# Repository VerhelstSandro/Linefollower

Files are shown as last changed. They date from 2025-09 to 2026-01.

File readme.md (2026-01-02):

# LineFollower

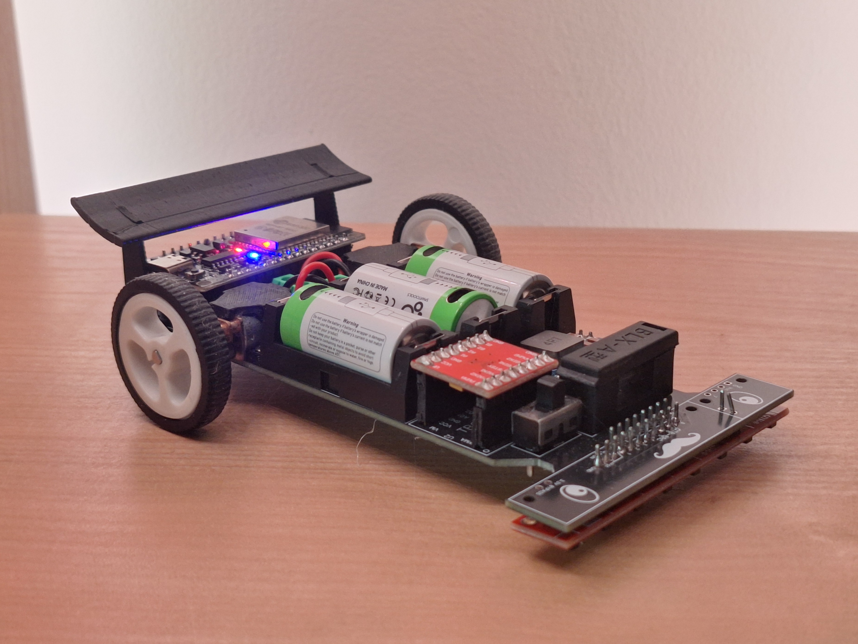
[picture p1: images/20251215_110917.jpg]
A description of my image


## specifications

microcontroller: ESP32 Wroom-32 devkit v1

motors: 12v n20 1000rpm

h-bridge: TB6612FNG

sensors: QTR-8A

batteries: RCR123A

wireless communication: ESP32

distance sensor - motors:

weight:

speed: 0.67 m/s

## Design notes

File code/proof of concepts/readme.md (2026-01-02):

# Proof of Concepts

De proof of concepts ben ik vergeten tonen in de fysieke lessen.

Bij de POC van de h brug is het enige wat niet werkt dat de linker motor niet achteruit kan draaien.
Dit komt omdat voor die motor achteruit te laten draaien er op de h brug bij Ain2 een hoog signaal moet zijn.
Deze is aangesloten op digitale pin18 van de esp en deze werkt jammer genoeg niet wanneer de SPI in gebruik is.
De SPI is in gebruik omdat ik met bluetooth werk. Ook als ik deze verwijder werkt het niet omdat de SPI automatisch opgestart wordt.

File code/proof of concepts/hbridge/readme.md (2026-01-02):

# H-Bridge proof of concept

## Werking van het programma:

1 - De linker motor gelijdelijk van stilstand tot de voorwaartse maximumsnelheid en blijft op deze snelheid draaien.

2 - De rechter motor gelijdelijk van stilstand tot de voorwaartse maximumsnelheid en blijft op deze snelheid draaien.

3 - Bijde Motoren gaan gelijdelijk stoppen.

4 - De linker motor gelijdelijk van stilstand tot de achterwaartse maximumsnelheid en blijft op deze snelheid draaien.

5 - De rechter motor gelijdelijk van stilstand tot de achterwaartse maximumsnelheid en blijft op deze snelheid draaien.

6 - Bijde Motoren gaan gelijdelijk stoppen.

en repeat

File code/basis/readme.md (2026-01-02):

## basis programma

Er is geen vershil tussen het basis programma en het finaal programma.

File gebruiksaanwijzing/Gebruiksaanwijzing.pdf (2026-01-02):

# Gebruiksaanwijzing

# Linefollower Sandro Verhelst

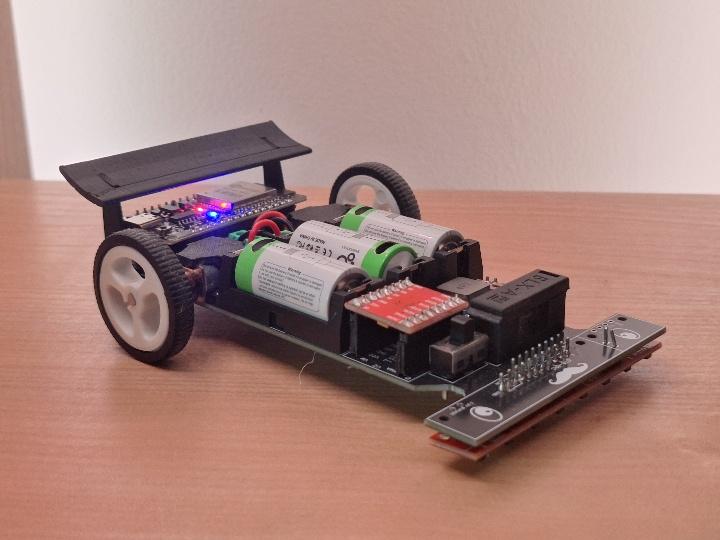
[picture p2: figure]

# Opladen / vervangen batterijen

De RCR123A batterijen die gebruikt zijn kunnen opgeladen worden via de usb-c poorten die op de batterijen aanwezig zijn met gelijk welke standaard usb-c lader.

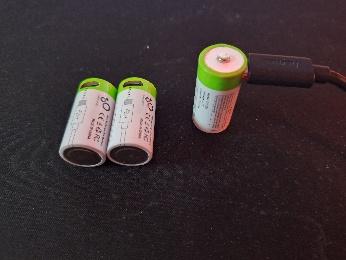
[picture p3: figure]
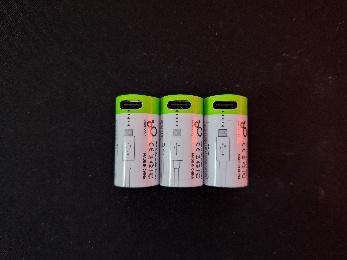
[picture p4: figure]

De batterijen zijn opgeladen zodra het rode lampje aan de plus pool groen is.

# draadloze communicatie

## verbinding maken

Voor het besturen en verbinding te maken met de linefollower is er een specifieke app gemaakt via androidstudio. De vereisten voor de app zijn simpel, een gsm met minimaal android 14.

Het APK-bestand is beschikbaar in de GitHub-repository onder de map “finaal”.
Download dit bestand naar je smartphone.

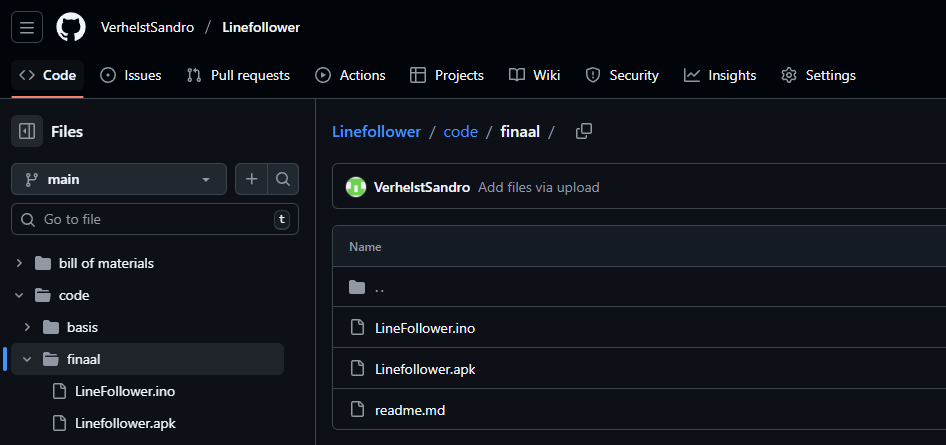
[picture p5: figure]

Open het gedownloade APK-bestand om de installatie te starten.

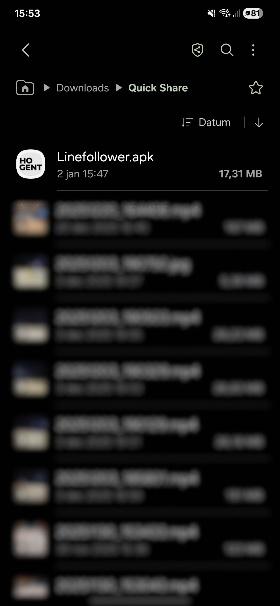
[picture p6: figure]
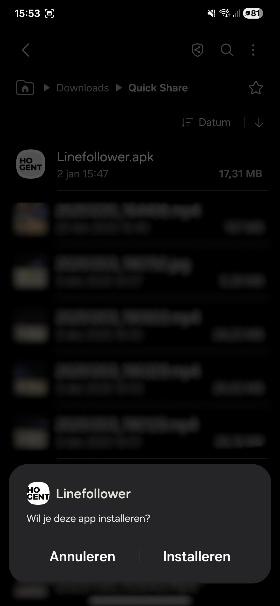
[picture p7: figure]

Bij de eerste installatie van een APK-bestand kan Android vragen om toestemming te geven aan de bestandsverkenner om applicaties van onbekende bronnen te installeren. Sta deze toestemming toe om verder te gaan.

Tijdens het installatieproces kan de antivirussoftware van de smartphone een waarschuwing weergeven. Voer in dat geval de controle uit en bevestig dat het bestand veilig is.

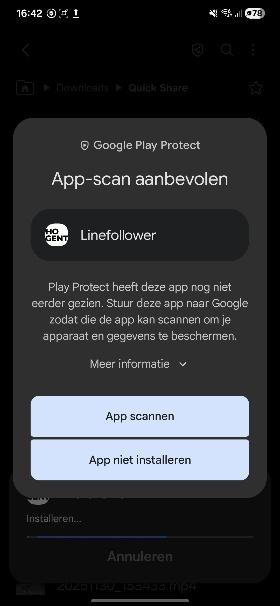
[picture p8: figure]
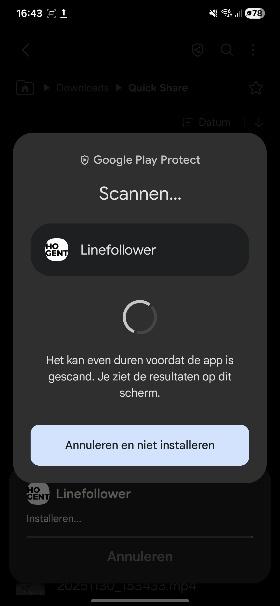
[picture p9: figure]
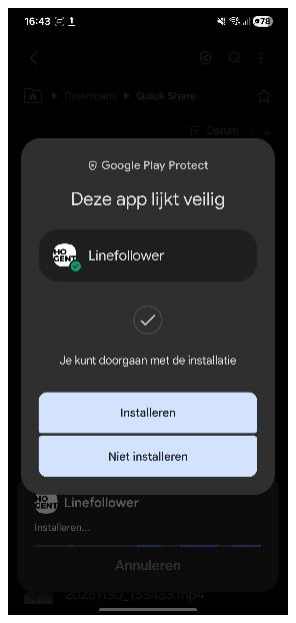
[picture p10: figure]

Na succesvolle installatie verschijnt de app in het overzicht van geïnstalleerde toepassingen.

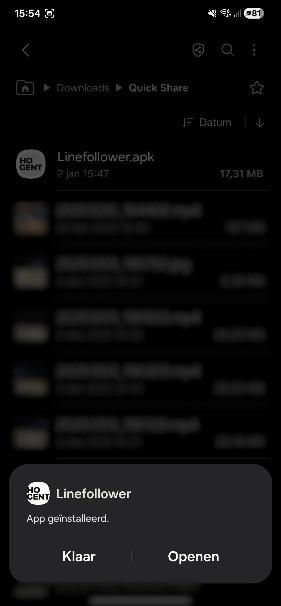
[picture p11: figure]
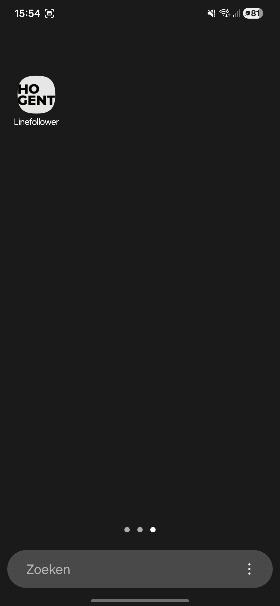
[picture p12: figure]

Zet de linefollower aan.

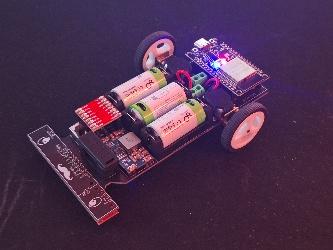
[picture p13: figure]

Activeer Bluetooth op de smartphone. Ga naar de Bluetooth-instellingen en zoek naar beschikbare apparaten. Selecteer de linefollower uit de lijst om verbinding te maken. Wanneer de verbinding tot stand is gebracht, verschijnt de linefollower als gekoppeld apparaat zonder dat die verbonden is.

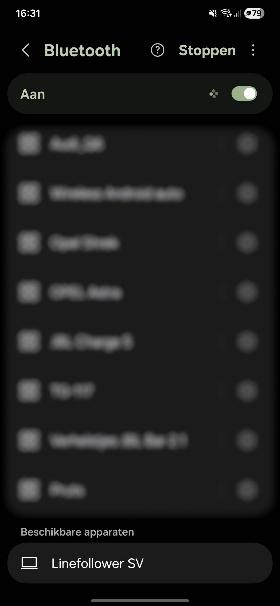
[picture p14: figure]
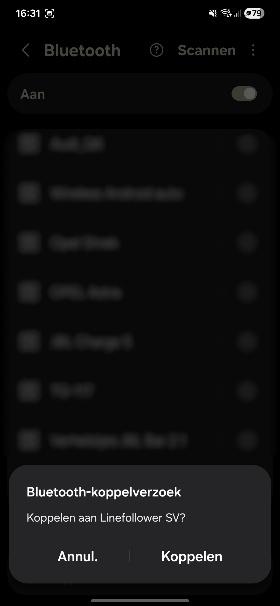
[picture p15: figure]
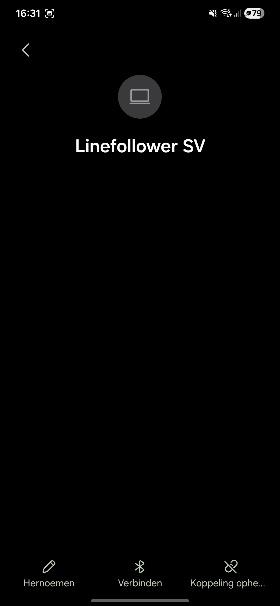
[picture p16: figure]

Open de geïnstalleerde app. Je komt terecht op het startscherm met de knop “Verbinden”. Druk op deze knop om verbinding te maken met de linefollower.

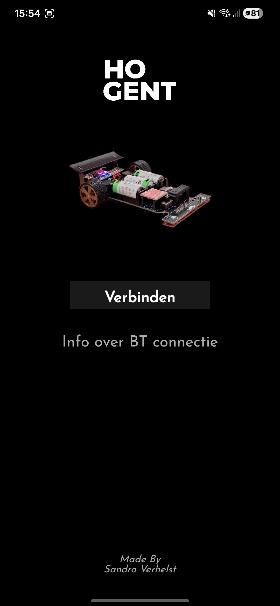
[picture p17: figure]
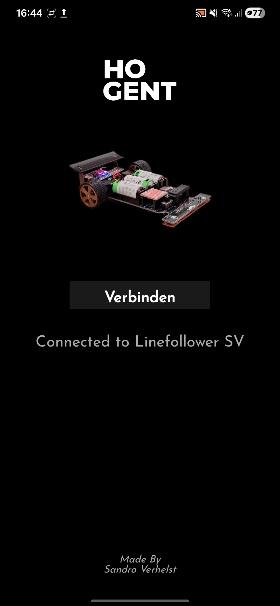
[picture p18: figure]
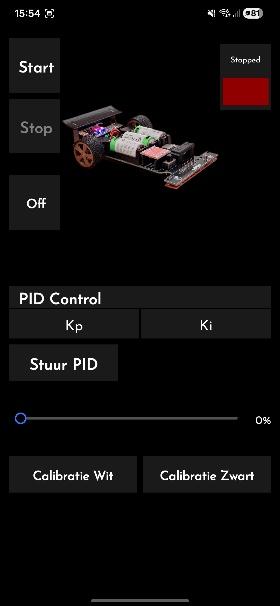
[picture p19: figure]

Na een succesvolle verbinding wordt automatisch het bedieningsscherm geopend. Vanuit dit scherm kan de linefollower volledig worden aangestuurd.

## commando's

aangezien ik met een custom app werk in plaats van commando’s ga ik gewoon uitleggen onder de commando’s hoe je dit doet in de app. Volgende foto voor referentie.

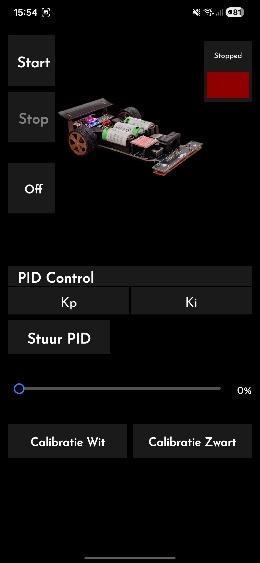
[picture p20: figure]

debug [on/off]

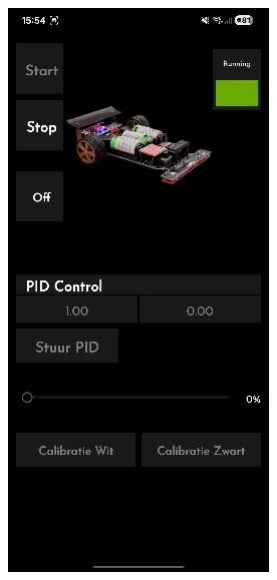
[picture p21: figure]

om te debuggen en waardes te zien moet je de via kabel de seriele poort gaan uitlezen dit kan niet via de app.

Start
Je hebt 2 mogelijkheden om start te bedienen. Start als “toggle button“ druk op start om te starten (dan kan je deze ook niet meer bedienen) en stop om te stoppen en de start knop als “dead man switch”. Door op de knop “off” te drukken toggle je tussen “off” (dead man switch off) en “hold” (hold to start). Als je nu wil starten moet je de knop blijven ingedrukt houden om de linefollower te doen rijden. Wanneer je loslaat stopt de linefollower direct.

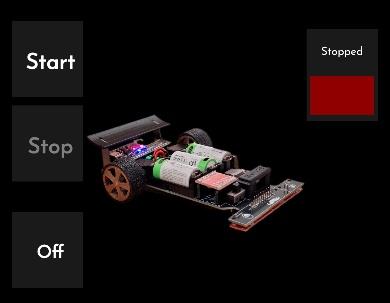
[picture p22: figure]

Stop
Je kan enkel de stop knop bedienen als de linefollower running is.

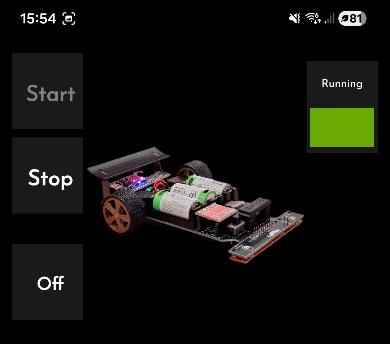
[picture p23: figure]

set cycle [µs]

Geen knop gemaakt wegens niet nodig.

set power [0..255]

Dit is in de app een slider onder stuur PID. De waarde van de snelheid is uitgedrukt in procent. Deze slider kan je niet bedienen als de Linefollower running is.

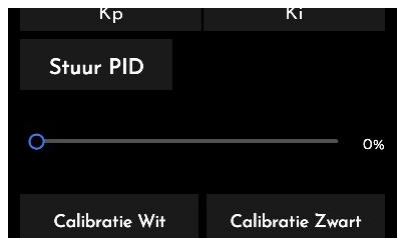
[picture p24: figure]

set kp [0..] en set ki [0..]

Deze waarden zet je door een waarde in te vullen in de vakken Kp en Ki. Door te drukken op Stuur PID worden de waarden aan de Linefollower gegeven. Deze knoppen kan je niet bedienen als de Linefollower running is.

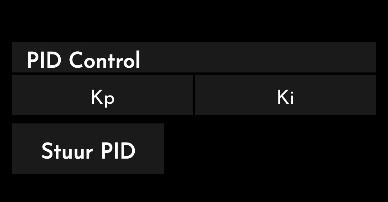
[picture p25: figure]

set kd [0..]

Geen knop gemaakt wegens niet nodig.

calibrate black en calibrate white

De twee knoppen onderaan. Door op deze knoppen te drukken kalibreer je de linefollower. De knoppen worden grijs als deze als het kleur dat de knop kalibreert al gekalibreerd is. Zo weet je dat je al gekalibreerd hebt, maar je kan de knoppen nog steeds bedienen als de linefollower niet running is.

# kalibratie

Je legt de linefollower aan en maakt verbinding via de app. Nu plaats je de robot op wit of zwart en druk je in de app op calibrate wit of calibrate zwart. Dit doe je voor bijde kleuren. Nu kan je rijden.

Indien de kalibratie die je gedaan hebt niet correct is gebeurd en je problemen ondervindt kan je steeds opnieuw op de knoppen drukken zelfs al zijn ze grijs.

De waarden worden niet opgeslaan in het eeprom geheugen omdat de app zodanig simpel is om te bedienen.

# settings

De robot rijdt stabiel met volgende parameters:

Kp = 0.9 en Ki = 0.05 bij goed opgeladen batterijen.

De robot is onder een groot bereik aan PI waardes zeer stabiel zelfs bij uitsluitend Ki (Kp = 0) met deze waarden mild beter dan de rest. Dit door een foutje in de code, het buitenste wiel gaat in een bocht sneller draaien dan de ingestelde snelheid. Dit wil zeggen dat als de snelheid over 50% gaat het buitenste wiel sneller dan 255 zou moeten draaien. Hierdoor wordt de auto boven 50% snelheid erg onstabiel. Door het grotere “potentieel” van de auto krijg je een groot bereik van PI waardes waar de auto onder 50% snelheid stabiel is.

# start/stop button

Er is geen fysieke start/stop button op de robot aanwezig.

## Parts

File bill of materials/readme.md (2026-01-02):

## bill of materials

Om de links te kunnen gebruiken moet je het bestand downloaden

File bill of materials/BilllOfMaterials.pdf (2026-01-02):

Onderdeel | Kwantiteit Prijs (€) | Link
1 | PCB Zelf Ontworpen | 1 | 1,40 | link (https://jlcpcb.com/)
2 | 12V N20 brushed DC motor 1000rpm | 2 | 4,54 | link (https://nl.aliexpress.com/item/1005005699205905.html?curPageLogUid=DE74yhz1LPuD)
3 | Esp32 WROOM-32 CH340C Type-C | 1 | 2,78 | link (https://nl.aliexpress.com/item/1005007465058316.html?curPageLogUid=niNGJFfweqLq)
4 | RCR123A usb-c | 3 | 13,86 | link (https://nl.aliexpress.com/item/1005009722694331.html?scm_id=1007.40050.354490.0&scm-url=1007.40050.354490.0)
5 | QTR-8A Lightsensor Array | 1 | 14,24 | link (https://eu.robotshop.com/nl/products/pololu-qtr-8a-reflectiesensor-array?qd=6190b6e8cdc3a3a41acff8d6a060cc69)
6 | TB6612FNG H-Brug | 1 | 0,86 | link (https://nl.aliexpress.com/item/1005006983040834.html?curPageLogUid=MGbjsEI1NrGM)
7 | Mini560 5V converter | 1 | 0,86 | link (https://nl.aliexpress.com/item/1005009769162034.html?curPageLogUid=MUVn4r33elyg)
8 | N20 motor rubber wheel | 2 | 0,82 | link (https://nl.aliexpress.com/item/33026783171.html?curPageLogUid=mJTzqF6iUgMG)
9 | BLX-A Fuse holder with 3A fuse | 1 | 1,48 | link (https://nl.aliexpress.com/item/1005008894822999.html?curPageLogUid=zWu5wig2f5bO)
10 | SS12D10 3 pin switch 4,7mm | 1 | 0,86 | link (https://nl.aliexpress.com/item/1005006157115358.html?curPageLogUid=FUC6MlSj6Va9)
11 | Terminal Block 2P 5mm pitch | 2 | 2,58 | link (https://nl.aliexpress.com/item/1005006963044077.html?curPageLogUid=M5rtjTEsVcEI)
12 | 2Draads kabel 1m 0,3mm2 | 1 | 0,86 | link (https://nl.aliexpress.com/item/1005010364473810.html?curPageLogUid=vg1IIguW8vi6)
13 | Male & Female Headers 2,58mm | 1 | 0,86 | link (https://nl.aliexpress.com/item/4000873858801.html?curPageLogUid=qPAsB0Q1JZVo)
14 | esun Black PLA | 10,19g | 0,12 | link (https://www.amazon.com.be/-/nl/PLA-filament-maatnauwkeurigheid-spoel-3D-printers-zwart/dp/B0CR1DBBFN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)
Totaal | 46,12

# Bill Of Materials

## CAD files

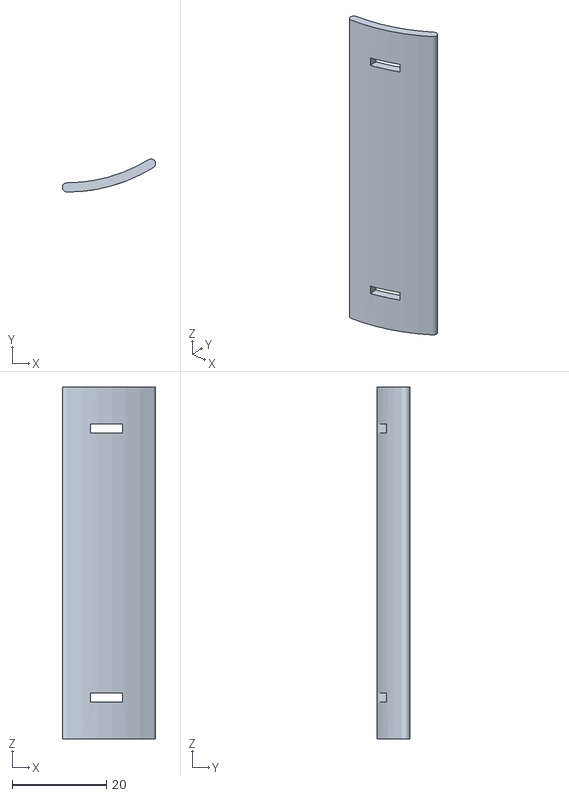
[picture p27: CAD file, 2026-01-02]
technische tekeningen/mechanisch/Spoiler.STL
19.8 x 7.04 x 74.8

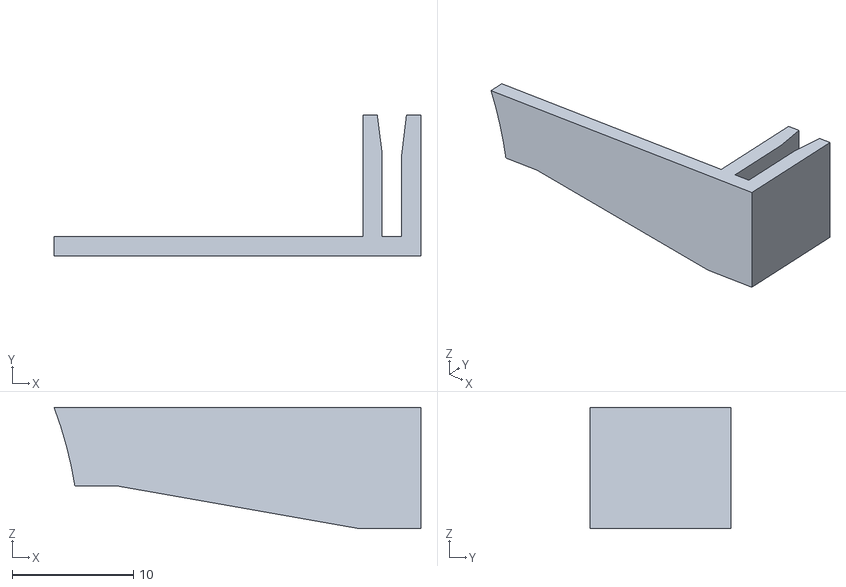
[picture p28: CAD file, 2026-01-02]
technische tekeningen/mechanisch/Spoiler Base.STL
30.3 x 11.6 x 10.0

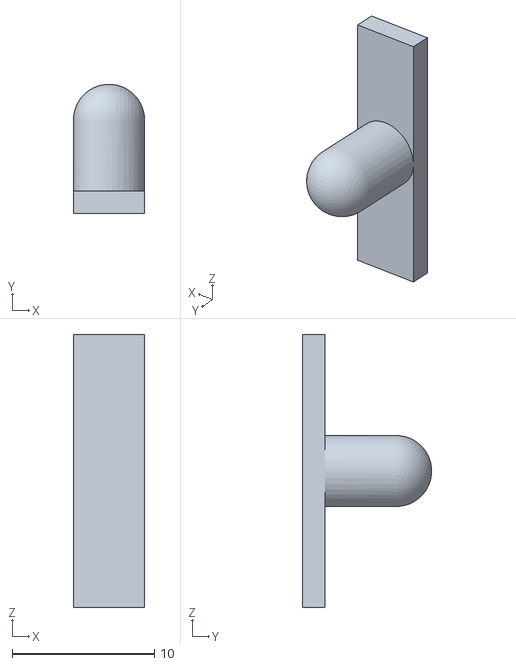
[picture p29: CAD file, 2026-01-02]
technische tekeningen/mechanisch/Caster.STL
5.00 x 9.09 x 19.2

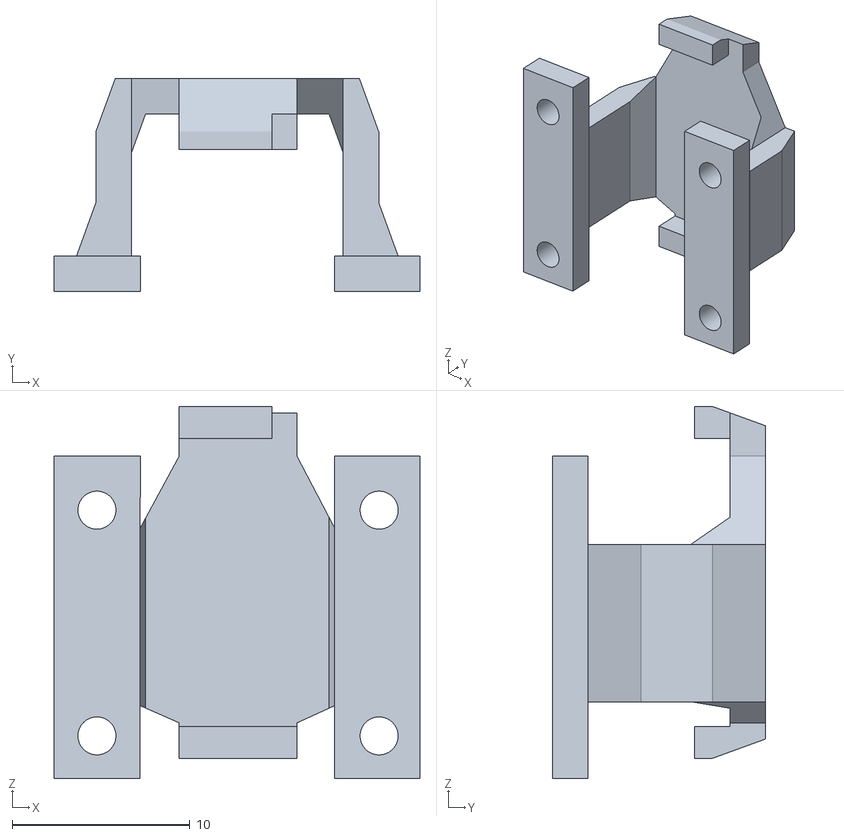
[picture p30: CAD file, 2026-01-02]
technische tekeningen/mechanisch/Motor Housing.STL
20.6 x 12.0 x 20.9

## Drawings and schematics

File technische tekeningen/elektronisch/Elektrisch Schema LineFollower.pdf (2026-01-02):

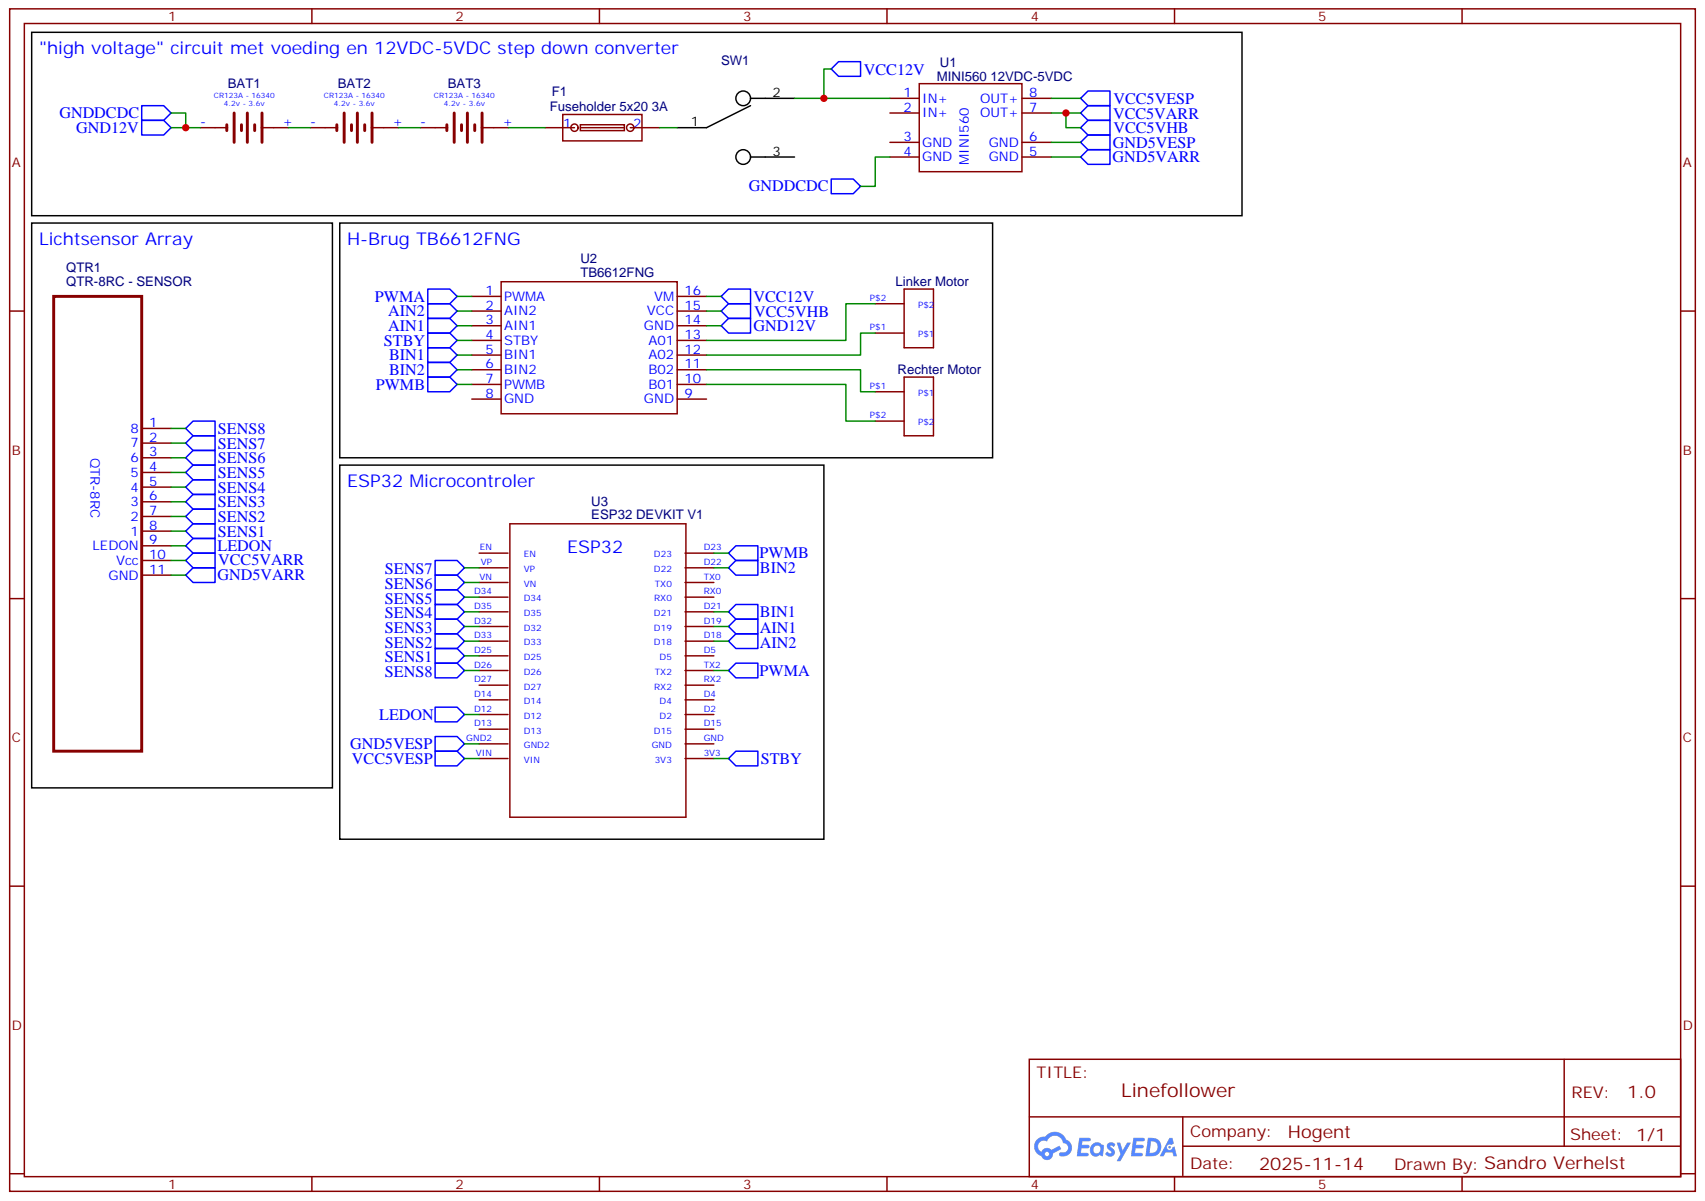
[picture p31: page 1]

"high voltage" circuit met voeding en 12VDC-5VDC step down converter

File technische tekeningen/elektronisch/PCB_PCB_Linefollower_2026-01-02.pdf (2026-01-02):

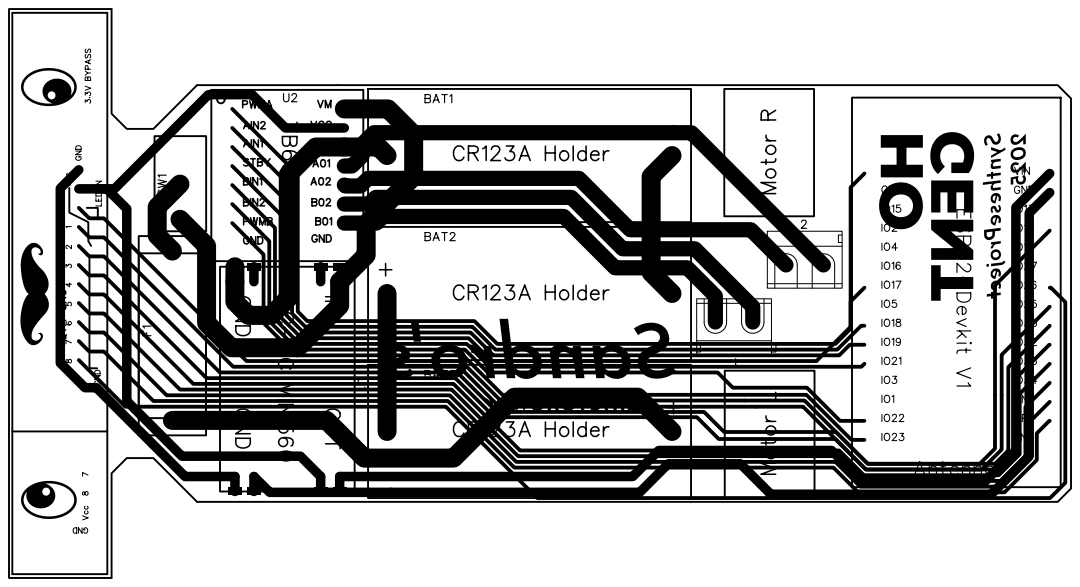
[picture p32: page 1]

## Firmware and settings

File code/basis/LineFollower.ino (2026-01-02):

#include "BluetoothSerial.h"

BluetoothSerial SerialBT;

//Linker Motor
#define PWMA 17
#define AIN1 19  //Vooruit
#define AIN2 18

//Rechter Motor
#define PWMB 23
#define BIN1 21
#define BIN2 22  //Vooruit

//status LED
#define LED 2

//Linesensor Array
#define SENS8 26
#define SENS7 36
#define SENS6 39
#define SENS5 34
#define SENS4 35
#define SENS3 32
#define SENS2 33
#define SENS1 25

#define SENSLED 12


//zelf gemaakte' variabelen
bool led = false;
unsigned long currentMillis;
unsigned long previousMillis;
unsigned long safcurrentMillis;
unsigned long safpreviousMillis;
float output;
int position;


int wit[8] = { 0, 0, 0, 0, 0, 0, 0, 0 };
int zwart[8] = { 4095, 4095, 4095, 4095, 4095, 4095, 4095, 4095 };
int offset[8];
float scaleInt[8];
int sensPins[8] = { SENS1, SENS2, SENS3, SENS4, SENS5, SENS6, SENS7, SENS8 };
int sens[8];
int norm[8];
int tot;

const int8_t weights[8] = { -35, -25, -15, -5, 5, 15, 25, 35 };

//variabelen voor BT
float Kp = 1, Ki = 0;
int v;
bool running = false;

//--------------------------------------------=-==- SETUP -==-=---------------------------------------------------------
void setup() {
  Serial.begin(115200);
  SerialBT.begin("ESP32_BT");  // verander naam indien nodig
  Serial.println("ESP32 BT ready");

  pinMode(PWMA, OUTPUT);
  pinMode(AIN1, OUTPUT);
  pinMode(BIN2, OUTPUT);

  pinMode(PWMB, OUTPUT);
  pinMode(BIN1, OUTPUT);
  pinMode(PWMA, OUTPUT);

  pinMode(LED, OUTPUT);

  pinMode(SENSLED, OUTPUT);
}

//--------------------------------------------=-==- LOOP -==-=---------------------------------------------------------
void loop() {


  // Lees berichten van Bluetooth
  if (SerialBT.available()) {
    String line = SerialBT.readStringUntil('\n');
    line.trim();
    handleCommand(line);
    Serial.println(line);
  }

  if (running == 1) {
    //============================== RUNNING ==============================

    //safpreviousMillis = 0;

    sensorRead();

    float pos = 0;
    for (int i = 0; i < 8; i++) {
      pos += norm[i] * (-3.5 + i);  // integer * int8_t
    }

    pos = (float)pos / (float)1000;

    if(norm[0] > (tot*0.9)){
      pos = -4.5;
    }
    else if(norm[7] > (tot*0.9)){
      pos = 4.5;
    }
    
    if (tot < 5000){
      /* proportioneel regelen */
      output = pos * Kp;

      /* integrerend regelen */
      output += Ki * pos;
    }
    else {
      output = 0;
    }

    output = clamp(output, -1, 1);

    int leftmotor = v * clamp((1 - output), 0, 1);
    int rightmotor = v * clamp((1 + output), 0, 1);

    analogWrite(PWMA, leftmotor);
    analogWrite(PWMB, rightmotor);

    /*
    currentMillis = millis();

    if (currentMillis - previousMillis > 100) {
      previousMillis = currentMillis;
      Serial.printf("%d,%d,%d,%d,%d,%d,%d,%d\n", norm[0], norm[1], norm[2], norm[3], norm[4], norm[5], norm[6], norm[7]);
      Serial.printf("totaal = %d\n", tot);
      Serial.printf("position = %.3f\n", pos);
      Serial.printf("output = %.3f, R=%d-L=%d\n", output, rightmotor, leftmotor);
    }
    
    */

  } else {
    //============================== STOPPED ==============================

    currentMillis = millis();

    digitalWrite(SENSLED, LOW);

    digitalWrite(AIN1, LOW);
    digitalWrite(AIN2, LOW);
    analogWrite(PWMA, 0);

    digitalWrite(BIN1, LOW);
    digitalWrite(BIN2, LOW);
    analogWrite(PWMB, 0);

    safpreviousMillis = 0;

    if (currentMillis - previousMillis > 500) {
      previousMillis = currentMillis;
      if (led == false) {
        digitalWrite(LED, HIGH);
        led = true;
      } else {
        digitalWrite(LED, LOW);
        led = false;
      }
    }
  }
}

//--------------------------------------------=-==- FUNCTIES -==-=---------------------------------------------------------

//============================== ANAOLOGE INGANGEN LEZEN & normalizeren ==============================
void sensorRead() {
  tot = 0;
  for (int i = 0; i < 8; i++) {
    sens[i] = analogRead(sensPins[i]);
    norm[i] = map(sens[i], wit[i], zwart[i], 0, 1000);
    tot += norm[i];
  }
}


//============================== BT LEZEN ==============================
void handleCommand(const String &cmd) {
  if (cmd.startsWith("CMD:")) {
    String c = cmd.substring(4);
    if (c == "RUN") {
      running = true;
      SerialBT.println("STATUS:RUNNING");
      SerialBT.printf("PID:Kp=%.2f,Ki=%.2f\n", Kp, Ki);

      digitalWrite(LED, HIGH);
      digitalWrite(SENSLED, HIGH);

      digitalWrite(AIN1, HIGH);
      digitalWrite(AIN2, LOW);

      digitalWrite(BIN1, LOW);
      digitalWrite(BIN2, HIGH);

    } else if (c == "STOP") {
      running = false;
      SerialBT.println("STATUS:STOPPED");
    }
  } else if (cmd.startsWith("PAR:")) {
    String c = cmd.substring(4);
    if (c.startsWith("SPEED=")) {
      parseAndSetSpeed(cmd.substring(4));

    } else if (c.startsWith("CAL_WHITE")) {
      // Kalibratie WIT ==============================
      digitalWrite(SENSLED, HIGH);
      delay(100);

      sensorRead();
      for (int i = 0; i < 8; i++) {
        wit[i] = sens[i];
      }
      SerialBT.println("STATUS:CALIBRATED_WHITE");

      digitalWrite(SENSLED, LOW);

    } else if (c.startsWith("CAL_BLACK")) {
      // Kalibratie ZWART ==============================
      digitalWrite(SENSLED, HIGH);
      delay(100);

      sensorRead();
      for (int i = 0; i < 8; i++) {
        zwart[i] = sens[i];
      }
      SerialBT.println("STATUS:CALIBRATED_BLACK");

      digitalWrite(SENSLED, LOW);
    }
  } else if (cmd.startsWith("PID:")) {
    parseAndSetPID(cmd.substring(4));
    SerialBT.printf("PID:Kp=%.4f,Ki=%.4f\n", Kp, Ki);
  }
}

//============================== SNELHEID LEZEN ==============================
void parseAndSetSpeed(String body) {
  int idx;
  idx = body.indexOf("SPEED=");
  if (idx >= 0) v = map(body.substring(idx + 6, body.indexOf(',', idx) > 0 ? body.indexOf(',', idx) : body.length()).toInt(), 0, 100, 0, 255);
}

//============================== PID LEZEN ==============================
void parseAndSetPID(String body) {
  int idx;
  idx = body.indexOf("Kp=");
  if (idx >= 0) Kp = body.substring(idx + 3, body.indexOf(',', idx) > 0 ? body.indexOf(',', idx) : body.length()).toFloat();
  idx = body.indexOf("Ki=");
  if (idx >= 0) Ki = body.substring(idx + 3, body.indexOf(',', idx) > 0 ? body.indexOf(',', idx) : body.length()).toFloat();
}


float clamp(float value, float min, float max) {
  if (value > max) {
    value = max;
  } else if (value < min) {
    value = min;
  }
  return value;
}

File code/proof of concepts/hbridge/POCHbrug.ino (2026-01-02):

/*
---------------------------------==-=- Proof Of concept H-Brug -=-==---------------------------------
*/

#include <SPI.h>

//Linker Motor
#define PWMA 17
#define AIN1 19  //Vooruit
#define AIN2 18

//Rechter Motor
#define PWMB 23
#define BIN1 21
#define BIN2 22  //Vooruit

//status LED
#define LED 2

//--------------------------------------------=-==- SETUP -==-=---------------------------------------------------------
void setup() {
  SPI.end();

  pinMode(PWMA, OUTPUT);
  pinMode(AIN1, OUTPUT);
  pinMode(BIN2, OUTPUT);

  pinMode(PWMB, OUTPUT);
  pinMode(BIN1, OUTPUT);
  pinMode(PWMA, OUTPUT);

  pinMode(LED, OUTPUT);
}

//--------------------------------------------=-==- LOOP -==-=---------------------------------------------------------
void loop() {
  digitalWrite(LED, HIGH);
  
  digitalWrite(AIN1, HIGH);
  digitalWrite(AIN2, LOW);
  digitalWrite(BIN1, HIGH);
  digitalWrite(BIN2, LOW);

  for (int speed = 0; speed <= 255; speed += 1) {
    analogWrite(PWMA, speed);
    delay(15);
  }
  for (int speed = 0; speed <= 255; speed += 1) {
    analogWrite(PWMB, speed);
    delay(15);
  }
  delay(100);
  for (int speed = 255; speed >= 0; speed -= 1) {
    analogWrite(PWMA, speed);
    analogWrite(PWMB, speed);
    delay(5);
  }

  // ACHTERUIT
  digitalWrite(AIN1, LOW);
  digitalWrite(AIN2, HIGH);
  digitalWrite(BIN1, LOW);
  digitalWrite(BIN2, HIGH);

  for (int speed = 0; speed <= 255; speed += 1) {
    analogWrite(PWMA, speed);
    delay(15);
  }
  for (int speed = 0; speed <= 255; speed += 1) {
    analogWrite(PWMB, speed);
    delay(15);
  }
  delay(100);
  for (int speed = 255; speed >= 0; speed -= 1) {
    analogWrite(PWMA, speed);
    analogWrite(PWMB, speed);
    delay(5);
  }
}
